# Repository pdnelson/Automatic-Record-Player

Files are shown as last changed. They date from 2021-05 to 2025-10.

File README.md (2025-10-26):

# Automatic Turntable Introduction
This project is currently under construction separately from this repository. This repository is now obsolete, and will be left in a non-functional state.

This is a fully automatic turntable that plays 7", 10" or 12" records! The automatic capabilities are powered by an Arduino Nano Every, 2 stepper motors, and a bunch of sensors.
Some notes on this turntable include (see "Features, User Inputs and Routines" section for more details):
- Stereo RCA outputs for a receiver
  - Includes Ground line
- Able to fit any commercial cartridge
- 16 2/3, 33 1/3, 45 and 78-RPM speeds
  - Digital or analog speed monitoring on 7-segment display or strobe disc, respectively
- Automatic functionality
  - Returns tonearm to "home" position automatically after a record is finished
  - Other buttons that contain other pre-defined routines (play and pause) that the user must initiate
  - Output port to allow another device to execute commands and read statuses
- Standard PC 3-prong female plug in the back to allow hookup to 120v or 230v households
- Counterbalance weight to fine-tune tonearm weight
- Skate/Anti-skate weight to fine-tune horizontal drift

# Demo Videos

I went over some information of this version of the turntable [in this video](https://www.youtube.com/watch?v=k4UXI1rkMYs). Further updates will be referenced on that channel.

# Features, User Inputs and Routines
The turntable has several inputs the user can use. Most of these functions must be initiated by the user by either pressing a button or flipping a switch, though homing can also be done automatically, which will be explained in more detail later on. Routine interrupt is currently not planned. This means that while one routine is running, none of the others can be executed for the duration of the currently-running routine.

## Automatic/manual switch
This is a 3-position switch with the center position being "off." Flipping the switch to the "up" position will set the turntable to automatic, while "down" will set it to manual. The turntable will automatically be homed upon flipping the switch to "automatic." Flipping it to "manual" will home the vertical axis, which will set the tonearm down in place where it currently is. The reason for this inclusion is to account for us not knowing what position the tonearm will be in when the device is turned on.

As soon as this switch is flipped to "manual" or "automatic," the software setup procedure begins.

## Play/Home button
The "play/home" button will pick the tonearm up from any point, and either drop it at the beginning of a record, or at the home position. If the tonearm is past the play position (i.e. on a record), then the button will home the tonearm. Otherwise, the button will drop it at the beginning of a record. These positions are determined using a slotted optical sensor.

## Pause button
The pause button will lift the tonearm up until the pause limit switch becomes "high." 

When the pause button is pressed again, if the tonearm is directly above "home" position, it will be set fown quickly until the lower limit switch becomes "high." Otherwise, if it is NOT over "home," it will be gently set down.

## Speed Selectors
There are two speed selector switches: The main selector switch, and the "alternate" speed button.

The main speed selector switch is a 3-position switch with the center position turning the turntable motor off, the lower position spinning it at 33 1/3-RPM, and the upper position spinning it at 45-RPM. When the "alternate" speed button is pressed, the switch's upper position will spin at 78-RPM, and the lower will spin at 16 2/3 RPM.

## Fine-Tune Speed Adjustment
On the right side of the record player, there are four potentiometers: One for each speed setting. This allows the user to perfectly dial in the speed they are looking to play at.

## Record size selector
The record size selector is a 3-position switch, with the top indicating 12", middle 10" and lower 7" records. This switch activates user-set calibration values for how many steps the tonearm should move past the play sensor to the edge of the record.

## Calibration Button
When the calibration button is pressed, the seven-segment display will display the active calibration value set by the record size selector. This value will indicate the number of steps taken once the tonearm moves past the play sensor during the play routine. In addition to showing the calibration value, this will also cause the pause button to increment the value, and the play button to decrement it. This can be used to fine-tune exact step calibrations, so the tonearm always lands on the correct spot of the record.

Releasing this button will save the setting to the Arduino's EEPROM. If the value is changed, saving will be indicated by the movement status LED flashing briefly.

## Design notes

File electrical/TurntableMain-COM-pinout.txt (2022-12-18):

1 - NC
2 - NC
3 - Output - Repeat button status
4 - Output - GND
5 - Output - Speed switch status
6 - Output - Automatic switch status
7 - Input - Play command
8 - Input - Pause command
9 - Input - Move turntable
10 - Input - Alt. Speed Set
11 - Output - Alt. speed status
12 - Input - Speed set
13 - Output - Pause status
14 - Output - Movement status
15 - Output - 5v
16 - Output - Home status

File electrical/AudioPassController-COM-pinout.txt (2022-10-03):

1 - Audio off (high = off, low = on)
2 - 5v
3 - GND

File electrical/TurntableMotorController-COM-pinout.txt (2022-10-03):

1 - Speed select A
2 - Speed select B
3 - Turntable power logic
4 - GND
5 - 12v in

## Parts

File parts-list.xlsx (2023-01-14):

Part Name/URL | Details | Qty. Included | Qty. Needed | Remaining Qty. | Price (Total) | Seller | Notes
Slotted Optical Sensor (https://www.amazon.com/gp/product/B08977QFK5/ref=ppx_yo_dt_b_asin_title_o07_s02?ie=UTF8&psc=1) |  | 5 | 1 | 4 | $8.99 | Amazon
Female RCA Panel-Mount Plugs (https://www.amazon.com/gp/product/B093YX4L9X/ref=ox_sc_act_image_1?smid=AQNSZ4MS7YO2W&psc=1) |  | 6 | 3 | 3 | $9.99 | Amazon
Dowel Pin (https://www.mcmaster.com/98381A510/) | 4037, 4140 Alloy Steel, 3/16" Diameter, 1" Long | 50 | 1 | 49 | $11.80 | McMaster |  | Total Price: | $675.67
Black-Oxide Alloy Steel Socket Head Screw (https://www.mcmaster.com/91251A106/) | 4-40 Thread Size, 1/4" Long | 100 | 20+ | 80- | $10.63 | McMaster
18-8 Stainless Steel Square Nut (https://www.mcmaster.com/94785A511/) | 4-40 Thread Size | 100 | 20+ | 80- | $13.40 | McMaster
Black-Oxide Alloy Steel Socket Head Screw (https://www.mcmaster.com/91251A108/) | 4-40 Thread Size, 3/8" Long | 100 | 10+ | 90- | $10.46 | McMaster
Brass Decorative Round Head Slotted Screw (https://www.mcmaster.com/92453A081/) | 2-56 Thread Size, 1/2" Long | 100 | 20+ | 80- | $7.13 | McMaster
Low-Strength Steel Square Nut (https://www.mcmaster.com/94855A279/) | Zinc-Plated, 2-56 Thread Size | 100 | 20+ | 80- | $5.86 | McMaster
316 Stainless Steel Washer (https://www.mcmaster.com/90107A003/) | for Number 2 Screw Size, 0.094" ID, 0.25" OD | 100 | 10+ | 90- | $2.73 | McMaster
Multipurpose 6061 Aluminum Round Tube (https://www.mcmaster.com/9056K63-9056K634/) | 0.035" Wall Thickness, 3/8" OD |  | 1 |  | $13.72 | McMaster | 2ft length
Black-Oxide Alloy Steel Socket Head Screw (https://www.mcmaster.com/90044A111/) | 4-40 Thread Size, 1" Long, Fully Threaded | 25 | 1 | 24 | $8.68 | McMaster
Rotary Shaft (https://www.mcmaster.com/1265K64/) | 316 Stainless Steel, 8 mm Diameter, 200 mm Long | 1 | 1 | 0 | $25.53 | McMaster | Must cut approx. in half
8mm Ball Bearings (https://www.amazon.com/Bearings-Skateboard-Shielded-Miniature-Skateboards/dp/B07R7PR72H) |  | 10 | 2 | 8 | $9.95 | Amazon
DPDT On-Off-On Switch (https://www.amazon.com/mts-202-125VAC-Position-Toggle-Switch/dp/B0799KM8T6) |  | 10 | 2 | 8 | $7.99 | Amazon
Bubble Spirit Level (https://www.amazon.com/dp/B07NRG8HX6?psc=1&ref=ppx_yo2_dt_b_product_details) |  | 10 | 1 | 9 | $6.99 | Amazon
KF2510 Connector Kit (https://www.amazon.com/dp/B01M69TKAM?psc=1&ref=ppx_yo2_dt_b_product_details) |  |  |  |  | $11.99 | Amazon
Rainbow Ribbon Cable (https://www.amazon.com/dp/B0775WHBP5?psc=1&ref=ppx_yo2_dt_b_product_details) |  |  |  |  | $14.69 | Amazon
6 Pins Dual Row Sockets for Flat Ribbon Cable (https://www.amazon.com/dp/B00D57XC9Q?psc=1&ref=ppx_yo2_dt_b_product_details) |  | 25 | 2 | 23 | $10.75 | Amazon
8 Pins 2.54mm Socket for Flat Ribbon Cable (https://www.amazon.com/dp/B017CMPM1A?psc=1&ref=ppx_yo2_dt_b_product_details) |  | 25 | 1 | 24 | $10.95 | Amazon
Audio-Technica AT-VM95C Cartridge (https://www.amazon.com/Audio-Technica-AT-VM95C-Moving-Turntable-Cartridge/dp/B07JL2RTBX) |  |  | 1 | 0 | $39.00 | Amazon
Turntable cartridge wires (https://www.amazon.com/gp/product/B08YN2D358/ref=ppx_yo_dt_b_asin_title_o06_s00?ie=UTF8&th=1) |  | 1 (set) | 1 (set) | 0 (sets) | $4.23 | Amazon
Linear Actuator (https://www.amazon.com/Electric-High-Speed-sec-Weight-Intelligent-Automation/dp/B07ZJ4XJZP) | 12v 10mm range | 1 | 1 | 0 | $29.99 | Amazon
Screw Mount AC Power Inlet with Fuse Holder (https://www.amazon.com/CESS-Screw-Mount-Holder-Socket/dp/B01GBW8J8A?s=hi) |  | 4 | 1 | 3 | $7.49 | Amazon
Micro limit switches (https://www.amazon.com/gp/product/B073TYWX86/ref=ppx_yo_dt_b_asin_title_o05_s01?ie=UTF8&psc=1) |  | 25 | 2 | 23 | $6.99 | Amazon
Cherry MX Blue Key switch (https://www.amazon.com/gp/product/B07V4S3QDK/ref=ppx_yo_dt_b_asin_title_o04_s00?ie=UTF8&th=1) |  | 20 | 3 | 17 | $11.99 | Amazon
Rubber bushings for motor mount (https://www.amazon.com/gp/product/B07VNDTCQR/ref=ox_sc_act_title_1?smid=ASV3IVVEECBWP&psc=1) |  |  |  |  | $11.97 | Amazon
5v Stepper Motor set w/ IC (https://www.amazon.com/KOOKYE-28BYJ-48-Stepper-ULN2003-Arduino/dp/B019TOJRC4) | must be 5v version |  | 2 |  | $9.99 | Amazon
Mean Well 12v Power Supply (https://www.amazon.com/MEAN-WELL-RS-25-12-Supply-Single/dp/B00FRBMV3Q) | RS-25-12 12V 2.1 Amp |  | 1 |  | $14.47 | Amazon
LEDs (https://www.amazon.com/ELEGOO-Diffused-Assorted-Colors-Arduino/dp/B0739RYXVC) |  | 3 | 600 | 597 | $12.99 | Amazon
Custom Turntable Belt | ~??? circumference (measured from belt) |  | 1 |  | $35.00 |  | TODO: Price is not exact
2370 Tinted Plexiglass (https://www.amazon.com/gp/product/B07R64KXFB/ref=ppx_yo_dt_b_asin_title_o05_s00?ie=UTF8&psc=1) |  |  |  |  | $10.99 | Amazon | Must cut down to size
Heat shrink tubing (https://www.amazon.com/560PCS-Heat-Shrink-Tubing-Eventronic/dp/B072PCQ2LW?s=industrial) |  |  |  |  | $6.99 | Amazon
High-Temperature Dry-Running 841 Bronze Sleeve Bearing (https://www.mcmaster.com/9368T98/) | for 3/16" Shaft Diameter and 1/4" Housing ID, 1/4" Long |  | 5 |  | $3.35 | McMaster
Isolation Feet (https://www.amazon.com/gp/product/B08GNV4BV1/ref=ewc_pr_img_1?smid=A3DXW0NUYLHI2J&th=1) |  | 4 | 4 | 0 | $14.20 | Amazon
Micro USB B Male to USB B Female (https://www.amazon.com/Traovien-Printer-MacBook-Samsung-Printers/dp/B09CY6K156) |  | 1 | 1 | 0 | $7.58 | Amazon
Rubber O Rings (https://www.amazon.com/dp/B08DWHMH9V?psc=1&ref=ppx_yo2ov_dt_b_product_details) | (1x 2" I/D 2 1/4" O/D) (4x 1/4" I/D 3/8" O/D) |  |  |  | $13.99 | Amazon
MX1508 H-Bridge w/ components (https://www.amazon.com/dp/B075S368Y2?psc=1&ref=ppx_yo2ov_dt_b_product_details) |  | 5 | 1 | 4 | $14.99 | Amazon
DC100 Motor Alone (includes pulley) (https://www.originlive.com/shop/dc100-motor-alone.html) |  | 1 | 1 | 0 | $132.22 | Origin Live
R3-2RS Ball Bearing (https://www.mcmaster.com/60355K861/) | Sealed, Trade Number R3-2RS, for 3/16" Shaft Diameter |  | 3 |  | $11.73 | McMaster
6.3v AC Transformer (https://www.digikey.com/en/products/detail/triad-magnetics/F-313X/5032119) |  | 1 | 1 | 0 | $11.06 | DigiKey
Parallel port (https://www.digikey.com/en/products/detail/norcomp-inc/171-025-103L001/858135) | 171-025-103L001 | 1 | 1 | 0 | $1.69 | DigiKey
Encoder (https://www.digikey.com/en/products/detail/broadcom-limited/HEDS-9700-E50/2219906) |  | 1 | 1 | 0 | $15.42 | DigiKey
Thread (https://www.amazon.com/Singer-150-yard-Purpose-Polyester-Thread/dp/B000PSAMCI) | Only needed for internal anti-skate; any thread will do | 1 | 1 | 0 | $4.26 | Amazon
Music Wire Steel Extension Spring with Loop Ends (https://www.mcmaster.com/5108N117/) |  | 5 | 1 | 4 | $14.92 | McMaster
Corrosion-Resistant Curved Disc Springs (https://www.mcmaster.com/9716K18/) |  | 5 | 1 | 4 | $11.76 | McMaster
Ball Bearing 3/8" shaft diameter (https://www.mcmaster.com/60355K504/) |  |  | 2 |  | $11.78 | McMaster
18-8 Stainless Steel Washer (https://www.mcmaster.com/92141A011/) | for Number 10 Screw Size, 0.203" ID, 0.438" OD | 100 | 1 | 99 | $2.40 | McMaster

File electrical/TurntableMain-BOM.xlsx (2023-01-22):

Label(s) | Type | Value(s) | Part Number | Substitute Part # | Mounting Type | Mount Size/Package | Quantity | Price Est. | Notes
A1 | Arduino Nano Every |  | ABX00028 |  | THT (read notes) | DIP30 | 1 | $10.38 | Developer recommends using 30-pin DIP socket. DE37566 pins may need to be used.
C1, C5, C6, C7, C8, C9, C10, C12, C13, C14, C15, C17, C19, C21, C22, C23, C24 | Ceramic Capacitor | 0.1µF; 35V | C0603C104K4NACAUTO |  | SMD | 0603 | 17 | $1.48
C2, C3 | Electrolytic Capacitor | 100µF; 16v | n/a |  | SMD |  | 2 | -- | Take from MX1508 PCB
C20 | Ceramic Capacitor | 1µF; 16V | 0805YD105KAT2A |  | SMD | 0805 | 1 | $0.24
C4, C11 | Ceramic Capacitor | 10µF; 16V | GCM21BM8EE106KE08L |  | SMD | 0805 | 2 | $1.30
C16, C18 | Ceramic Capacitor | 47nF; 25v | 06033C473KAT2A |  | SMD | 0603 | 2 | $0.20
D1 | Diode |  | n/a |  | SMD |  | 1 | -- | Take from MX1508 PCB
D2 | Schottky Diode | 30v; 3a | B330AF-13 |  | SMD | DO-221AC, SMA | 1 | $0.44
J1 | Screw terminal - 2 pins |  | 691137710002 |  | THT |  | 1 | $0.41
J2 | generic male header - 1 pin (1 row) |  | DE37566 |  | THT |  | 1 | -- | Comes in lot listed on main parts list.
J4 | Generic shrouded header - 6 pins (2 rows) |  | 61200621621 | BHR-06-VUA | THT |  | 1 | $0.48
J3, J5, J9, J10, J11, J13, J14, J15, J17 | male header 2 pin (1 row) |  | KF2510 2-pin |  | THT |  | 9 | -- | Comes in a lot with other KF2510 connectors.
J6 | male header 5 pin (1 row) |  | KF2510 5-pin |  | THT |  | 1 | -- | Comes in a lot with other KF2510 connectors.
J7, J8 | male header 5 pins (1 row) |  | YXQJST-XH 4S |  | THT |  | 2 | -- | Comes in lot listed on main parts list.
J16, J18, J19 | male header - 3 pins (1 row) |  | KF2510 3-pin |  | THT |  | 3 | -- | Comes in a lot with other KF2510 connectors.
J12 | Generic shrouded header - 16 pins (2 rows) |  | SBH11-PBPC-D08-RA-BK |  | THT |  | 1 | $0.73
J20 | male header 4 pins (1 row) |  | KF2510 4-pin |  | THT |  | 1 | -- | Comes in a lot with other KF2510 connectors.
J21 | Generic shrouded header - 8 pins (2 rows) |  | BHR-08-VUA |  | THT |  | 1 | $0.35
R4 | Resistor | 220Ω | n/a |  | SMD | 0805 | 1 | -- | Take from MX1508 PCB
R2, R3, R4, R8, R9, R10, R11, R12, R13, R14, R15, R16 | Resistor | 10kΩ; ±5%; 1/4w | ERJ-PA3F1002V |  | SMD | 0603 | 12 | $1.68
R5, R6, R7 | Resistor | 1kΩ; ±5%; 1/4w | ERJ-PA3J102V |  | SMD | 0603 | 3 | $0.33
U1, U6 | Voltage Regulator - Linear | 5v; 3a | MIC29300-5.0WT | MIC29310-5.0WT | THT | TO220 | 2 | $9.40
U2, U3 | Power/Stepper driver |  | ULN2003A |  | THT (read notes) | DIP16 | 2 | -- | Developer recommends using 16-pin DIP socket
U4 | Motor driver |  | MX1508 |  | SMD |  | 1 | -- | Take from MX1508 PCB
U5 | 8:1 multiplexer |  | CD4051BE |  | THT |  | 1 | $0.79
U7, U10, U11, U12, U13, U14 | "Or" gate | 5v | MC74VHC1G32DTT1G |  | SMD | SC-74A, SOT-753 | 6 | $2.88
U8, U9 | "And" gate |  | SN74AUC1G08DCKR |  | SMD | SC-74A, SOT-753 | 2 | $0.98
U15, U16, U17, U18 | 1:2 demultiplexer |  | SN74LVC1G18DBVR |  | SMD | SOT-23-6 | 4 | $1.64
Total (where applicable): |  |  |  |  |  |  | 82 | $33.71
Notes:
Price estimates are as of 3 Sept. 2022

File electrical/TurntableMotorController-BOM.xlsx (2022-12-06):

Label(s) | Type | Value(s) | Part Number | Substitute Part # | Mounting Type | Mount Size/Package | Quantity | Price Est. | Notes
C1, C3 | Ceramic Capacitor | 10µF; 16V | GCM21BM8EE106KE08L |  | SMD | 0805 | 2 | $1.30
C2 | Ceramic Capacitor | 22µF; 25v | CL21A226MAYNNNE |  | SMD | 0805 | 1 | $0.25
C4 | Ceramic Capacitor | 0.47nF; 50v | 0805B471K500CT |  | SMD | 0805 | 1 | $0.10
C5, C6, C7, C8, C9, C10 | Ceramic Capacitor | 100 nf; 50v | CL21B104KBCNNNC |  | SMD | 0805 | 6 | $0.60
R5, R14, R15 | Resistor | 1kΩ; ±5%; 1/4w | ERJ-PA3J102V |  | SMD | 0603 | 3 | $0.33
R6, R10 | Resistor | 69kΩ | RN73H1JTTD6902D100 |  | SMD | 0603 | 2 | $0.78
R7 | Resistor | 26.7kΩ | RC0603FR-0726K7L |  | SMD | 0603 | 1 | $0.10
R8, R9 | Resistor | 47kΩ | RG1608P-473-B-T5 |  | SMD | 0603 | 2 | $0.76
R11 | Resistor | 104kΩ | RN73H1JTTD1043B50 |  | SMD | 0603 | 1 | $0.53
R12 | Resistor | 94kΩ | RT0603BRD0794K2L |  | SMD | 0603 | 1 | $0.34
R13 | Resistor | 10kΩ; ±5%; 1/4w | ERJ-PA3F1002V |  | SMD | 0603 | 1 | $0.16
U3, U4, U5, U6, U7, U8 | Demultiplexer 1:2 | 12v; 5a | ISL43210IHZ-T7A | DG9431EDV-T1-GE3 | SMD |  | 6 | $17.52
U2 | Variable Voltage Regulator | 12v; 5a | AZ1084CS2-ADJTRE1 |  | SMD |  | 1 | $0.72
D1 | Rectifier Diode |  | 1N4007 |  | THT | 300 mil | 1 | $0.11
Q1 | Basic FET P-Channel |  | TIP120 |  | THT |  | 1 | $1.00
U1 | Voltage Regulator - Linear | 5v; 3a | MIC29300-5.0WT | MIC29310-5.0WT | THT | TO220 | 1 | $4.70
R1, R2, R3, R4 | Thumbwheel Potentiometer | 10kΩ; 1/2w | 3352W-1-103LF |  | THT |  | 4 | $10.00
RL1 | Relay |  | J104D2C5VDC.20S |  | THT | DPDT (2 Form C) | 1 | $1.31
J1, J2, J3, J4 | Screw Terminal |  | 8191 | 36-8191-ND | THT |  | 4 | $2.08
J5 | male header 5 pins (1 row) |  | KF2510 5-pin |  | THT |  | 1 | --
J6 | male header 2 pins (1 row) |  | KF2510 2-pin |  | THT |  | 1 | --
J7 | Screw terminal (2 pins) |  | ED10563-ND |  | THT |  | 1 | $0.41
Total (where applicable): |  |  |  |  |  |  | 42 | $42.69
Notes:
Price estimates are as of 2 Oct. 2022

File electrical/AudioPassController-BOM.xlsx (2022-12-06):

Label(s) | Type | Value(s) | Part Number | Substitute Part # | Mounting Type | Mount Size/Package | Quantity | Price Est. | Notes
C1 | Ceramic Capacitor | 10µF | CL21A106KOQNNNE |  | SMD | 0805 | 1 | $0.10
C2 | Ceramic Capacitor | 1µF | CL21B105KAFNNNE |  | SMD | 0805 | 1 | $0.10
C3 | Ceramic Capacitor | 47nF | CL21B473KBCNNNC |  | SMD | 0805 | 1 | $0.10
C4, C5 | Ceramic Capacitor | 100nF | CL21B104KACNNNC |  | SMD | 0805 | 2 | $0.10
R1, R2 | Resistor | 10kΩ; ±5%; 1/4w | ERJ-PA3F1002V |  | SMD | 0603 | 2 | $0.32
U1, U2 | 1:2 demultiplexer |  | SN74LVC1G18DBVR |  | SMD | SOT-23-6 | 2 | $0.82
J1 | male header - 3 pins (1 row) |  | KF2510 3-pin |  | THT |  | 1 | --
J2 | Screw terminal (4 pins) |  | ED10563-ND |  | THT |  | 1 | $1.45
J3, J4 | male header - 2 pins (1 row) |  | KF2510 2-pin |  | THT |  | 2 | --
Total (where applicable): |  |  |  |  |  |  | 13 | $2.99
Notes:
Price estimates are as of 2 Oct. 2022

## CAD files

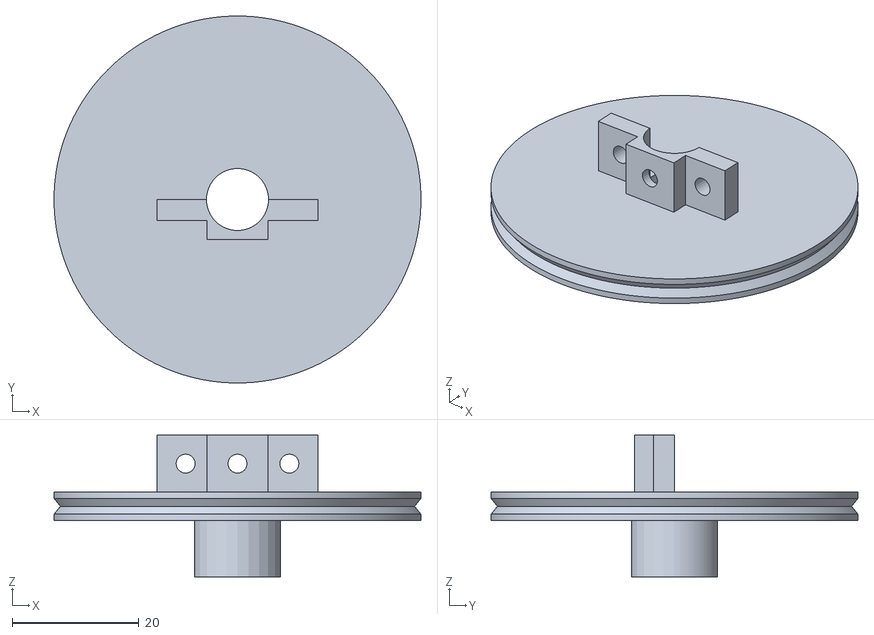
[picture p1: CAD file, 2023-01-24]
3d-models/tonearm-movement-hub/horizontal-movement/main-drive-wheel.stl
58.0 x 58.0 x 22.4

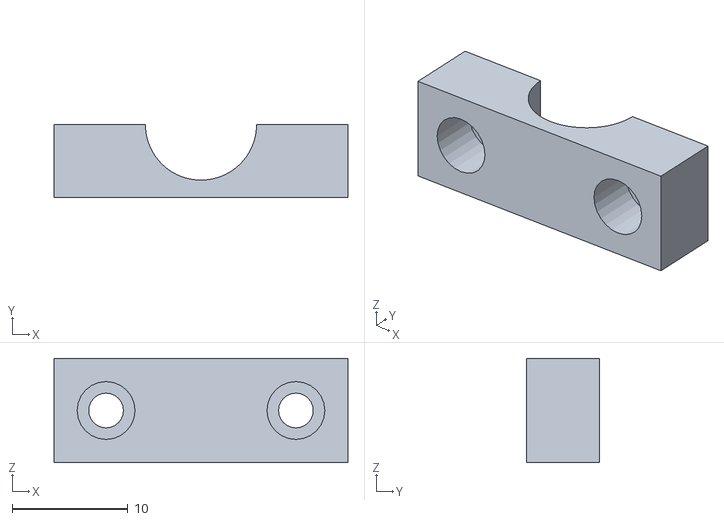
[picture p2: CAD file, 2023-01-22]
3d-models/tonearm-movement-hub/horizontal-movement/main-drive-wheel-fastener.stl
25.4 x 6.30 x 9.00

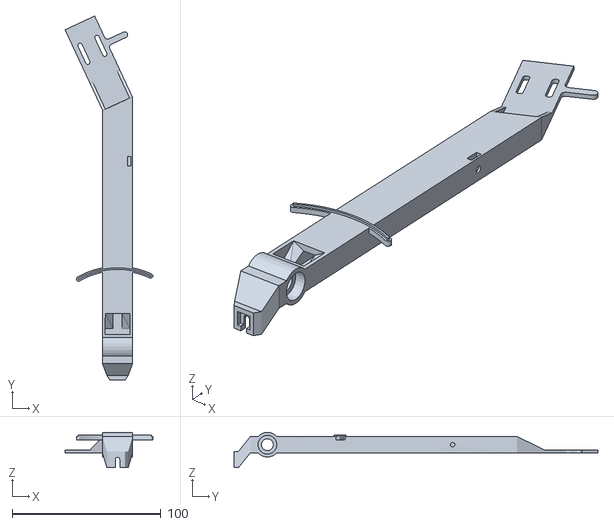
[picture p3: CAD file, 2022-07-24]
3d-models/tonearm/tonearm-full.stl
59.2 x 245.0 x 23.9

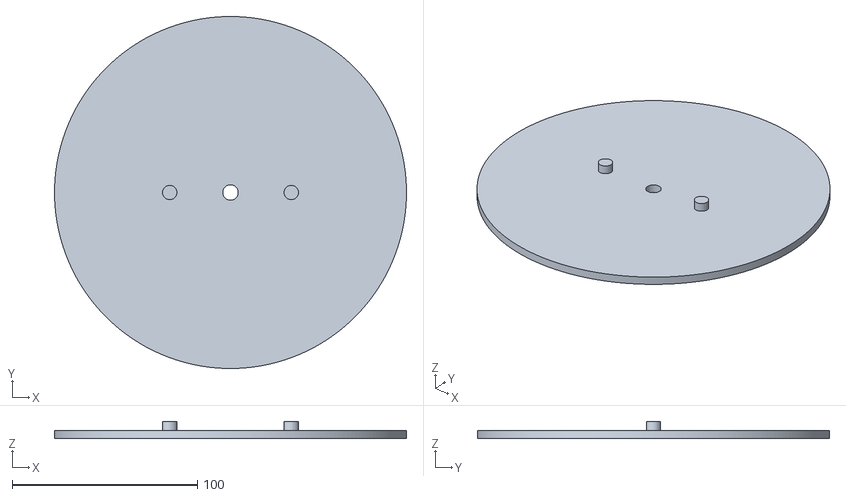
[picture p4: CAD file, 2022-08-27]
3d-models/turntable/turntable/full-platter.stl
190.0 x 190.0 x 9.30

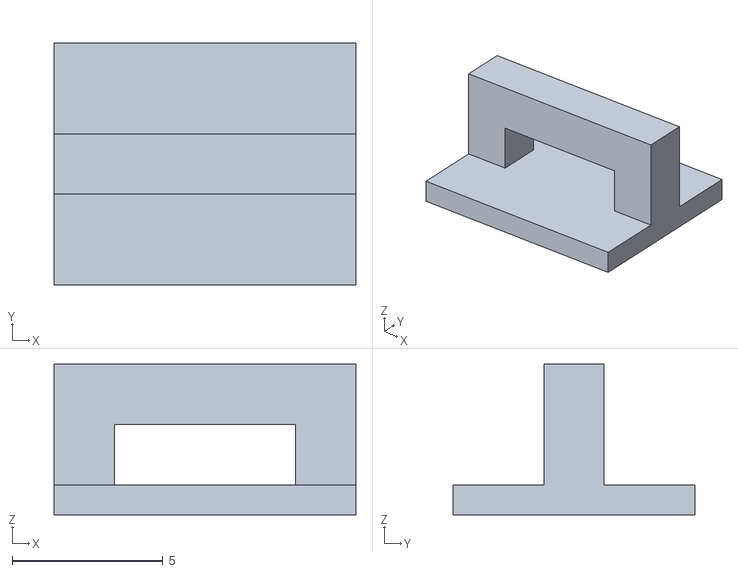
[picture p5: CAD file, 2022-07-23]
3d-models/cable-management-thing.stl
10.0 x 8.00 x 5.00

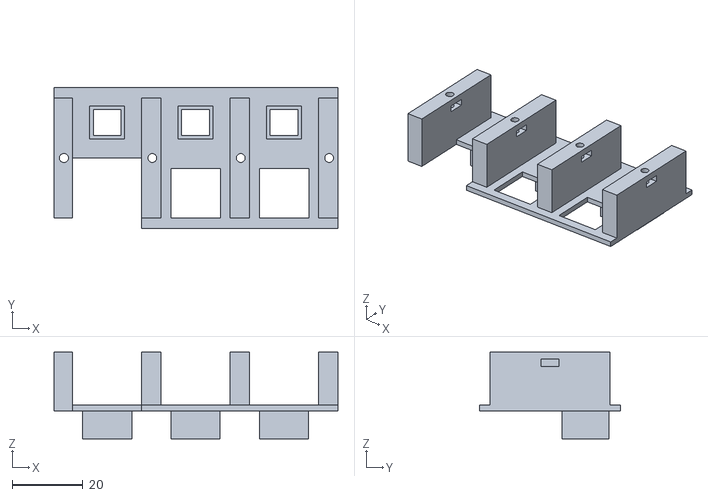
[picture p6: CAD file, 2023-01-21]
3d-models/command-buttons/command-button-holder.stl
80.3 x 40.0 x 24.5

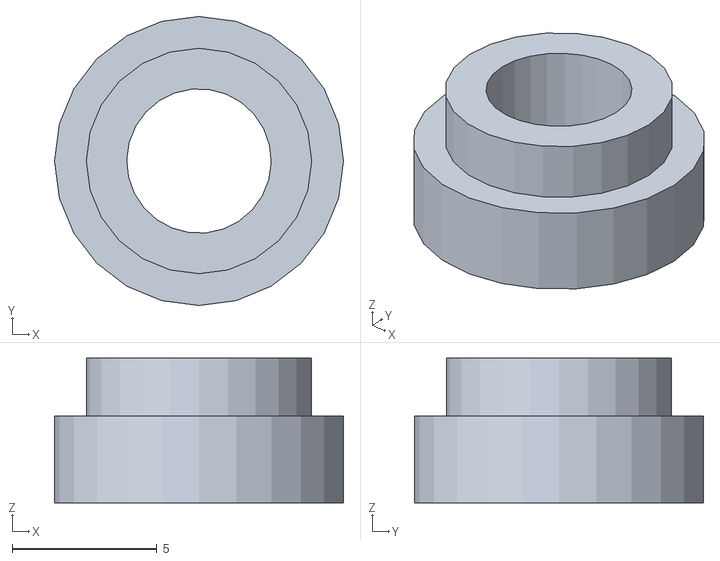
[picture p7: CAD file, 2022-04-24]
3d-models/inner-chassis/ir-sensor-mount/movement-ir-interrupter-spacer.stl
10.00 x 10.0 x 5.00

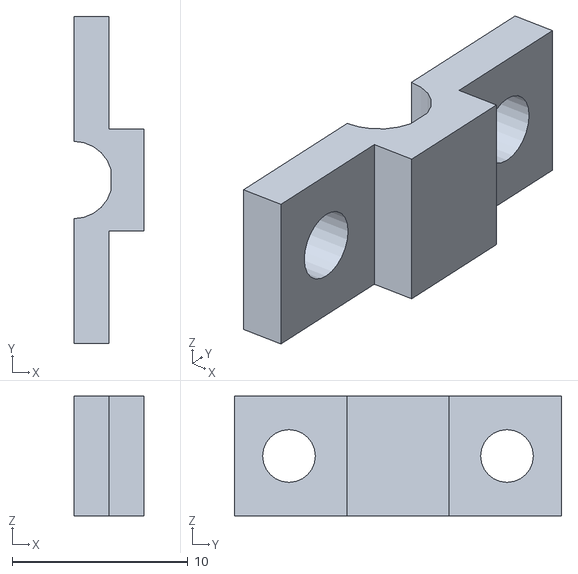
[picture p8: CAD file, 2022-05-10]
3d-models/inner-chassis/tonearm-rod-clip.stl
4.00 x 18.6 x 6.80

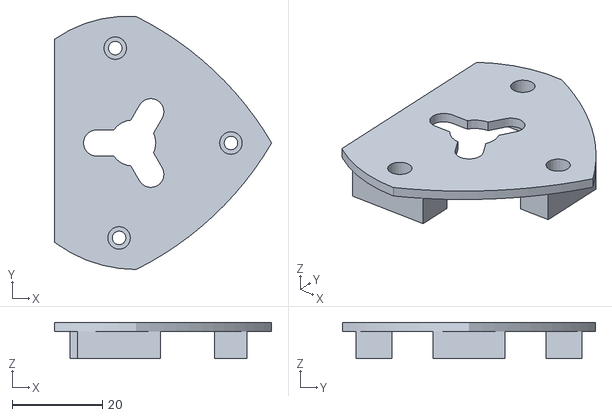
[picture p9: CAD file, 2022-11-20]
3d-models/motor-mount/motor-mount-one-piece-top.stl
48.1 x 56.0 x 8.00

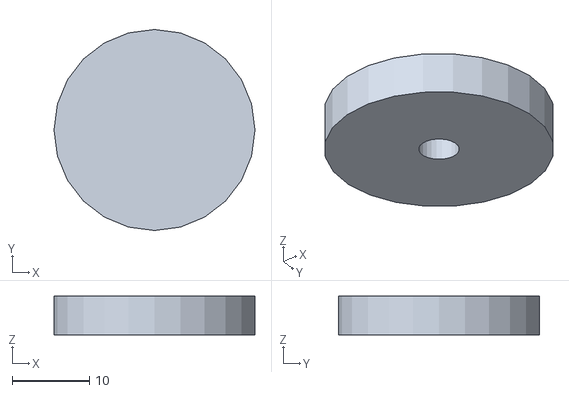
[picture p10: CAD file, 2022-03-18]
3d-models/shell/foot.stl
26.0 x 26.0 x 5.00

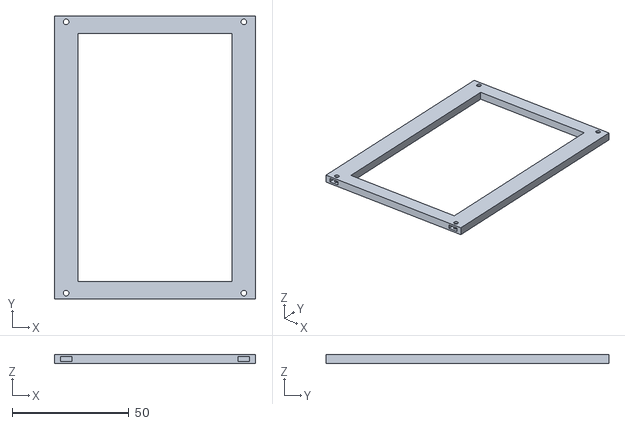
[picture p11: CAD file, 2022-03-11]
3d-models/speed-adjustment-enclosure/speed-adjustment-enclosure-mount.stl
86.0 x 121.0 x 4.00

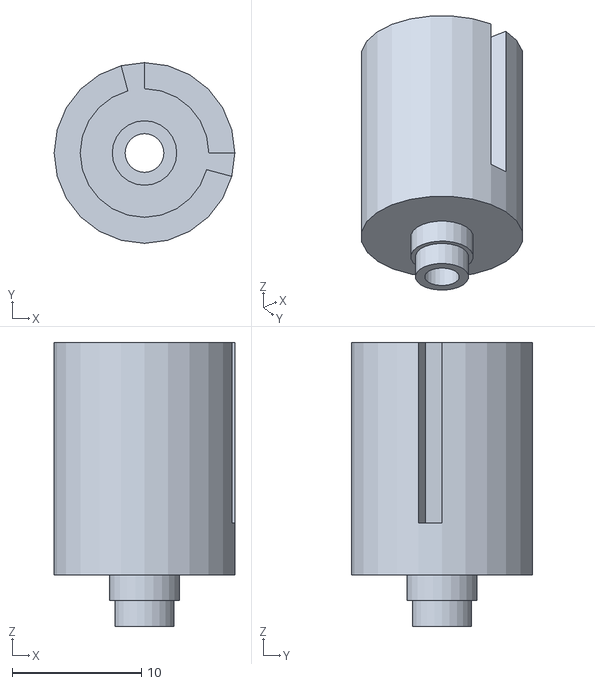
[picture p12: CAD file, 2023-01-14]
3d-models/tonearm-movement-hub/anti-skate/bottom-mechanism.stl
14.0 x 14.0 x 22.0

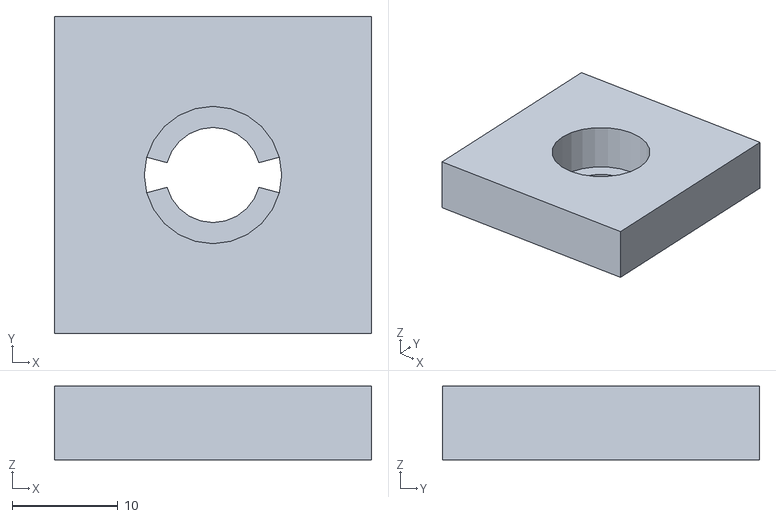
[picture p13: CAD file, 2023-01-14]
3d-models/tonearm-movement-hub/anti-skate/prototype/bearing-holder.stl
30.0 x 30.0 x 7.00

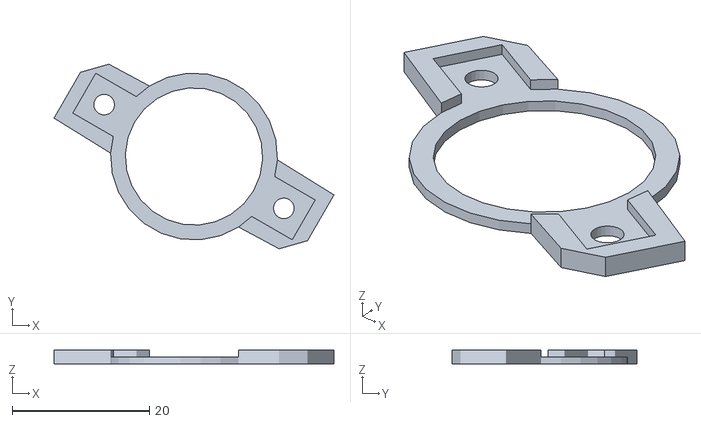
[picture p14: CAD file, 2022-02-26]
3d-models/tonearm-movement-hub/ball-bearing-components/ball-bearing-brace.stl
40.8 x 26.9 x 2.00

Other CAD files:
3d-models/tonearm-movement-hub/horizontal-movement/h-motor-mount/linear-actuator-bracket.stl
3d-models/tonearm-movement-hub/horizontal-movement/horizontal-axis-rod/horizontal-axis-rod-stencil-pt-2.stl
3d-models/tonearm-movement-hub/horizontal-movement/horizontal-axis-rod/prototype/h-axis-rod-prototype.stl
3d-models/tonearm-movement-hub/ir-interrupter/movement-ir-interrupter-fastener.stl
3d-models/cable-management-thing.skp
3d-models/command-buttons/button-cherry.skp
3d-models/command-buttons/button-cherry.stl
3d-models/command-buttons/button-push.skp
3d-models/command-buttons/button-push.stl
3d-models/command-buttons/command-button-holder.skp
3d-models/command-buttons/command-button-stencil.skp
3d-models/command-buttons/command-button-stencil.stl
3d-models/command-buttons/single-command-button-holder.skp
3d-models/command-buttons/single-command-button-holder.stl
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

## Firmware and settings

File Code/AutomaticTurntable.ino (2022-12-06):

#include <Stepper.h>
#include <Multiplexer.h>
#include <DcMotor.h>
#include "proto/AutomaticTurntable.h"
#include "proto/Constants.h"
#include "enums/ArduinoPin.h"
#include "enums/MultiplexerInput.h"
#include "enums/MovementResult.h"
#include "enums/AutoManualSwitchPosition.h"
#include "TonearmMovementController.h"

// Though this is one stepper motor declaration, this object actually handles both the vertical and horizontal
// stepper motors. Which one is currently active is determined by the ArduinoPin::MotorAxisSelector.
Stepper tonearmMotor = Stepper(
  STEPS_PER_REVOLUTION, 
  ArduinoPin::StepperPin4,
  ArduinoPin::StepperPin2, 
  ArduinoPin::StepperPin3, 
  ArduinoPin::StepperPin1
);

// The multiplexer monitors most input values that we read to determine the statuses of various sensors.
Multiplexer mux = Multiplexer(
  ArduinoPin::MuxOutput, 
  ArduinoPin::MuxSelectorA, 
  ArduinoPin::MuxSelectorB, 
  ArduinoPin::MuxSelectorC
);

// The tonearmClutch allows us to engage or disengage the horizontal gearing to either allow for automatic
// movement (engaged), or manual movement (disengaged).
DcMotor horizontalClutch = DcMotor(
  ArduinoPin::HorizontalClutchMotorDir1,
  ArduinoPin::HorizontalClutchMotorDir2
);

// The tonearmController is in charge of automatically moving the tonearm vertically or horizontally.
TonearmMovementController tonearmController = TonearmMovementController(
  mux,
  tonearmMotor,
  ArduinoPin::MotorAxisSelector,
  horizontalClutch,
  MultiplexerInput::VerticalLowerLimit,
  MultiplexerInput::VerticalUpperLimit
);

// All of these fields are used to calculate the speed that the turntable is spinning.
volatile unsigned long currMillisSpeed = millis();
volatile unsigned long lastMillisSpeed = currMillisSpeed;
volatile double currSpeed;

// Used for the pickup sensor
uint8_t consecutivePickupSensorChanges = 0;
bool lastPickupSensorStatus = false;
unsigned long lastMillisPickup = __LONG_MAX__;

bool paused = false;

void setup() { //Serial.begin(SERIAL_SPEED);
  // Set pins
  pinMode(ArduinoPin::MovementStatusLed, OUTPUT);
  pinMode(ArduinoPin::PauseStatusLed, OUTPUT);
  pinMode(ArduinoPin::SpeedSensor, INPUT);
  attachInterrupt(digitalPinToInterrupt(ArduinoPin::SpeedSensor), calculateTurntableSpeed, RISING);

  // Set calibration values
  tonearmController.setClutchEngagementMs(CLUTCH_ENGAGEMENT_MS);
  tonearmController.setTopMotorSpeed(MOVEMENT_RPM_TOP_SPEED);
  tonearmController.setVerticalTimeout(VERTICAL_MOVEMENT_TIMEOUT_STEPS);
  mux.setDelayMicroseconds(MULTIPLEXER_DELAY_MICROS);

  // Engage the horizontal clutch. This will be setting it to the "starting" point for where we know it is engaged
  horizontalClutch.immediateStart(HorizontalClutchPosition::Engage);

  // Begin startup light show
  delay(100);
  digitalWrite(ArduinoPin::PauseStatusLed, LOW);
  digitalWrite(ArduinoPin::MovementStatusLed, HIGH);
  delay(100);
  digitalWrite(ArduinoPin::MovementStatusLed, LOW);
  digitalWrite(ArduinoPin::PauseStatusLed, HIGH);
  delay(100);
  digitalWrite(ArduinoPin::MovementStatusLed, HIGH);
  digitalWrite(ArduinoPin::PauseStatusLed, LOW);
  delay(100);
  digitalWrite(ArduinoPin::MovementStatusLed, LOW);
  // End startup light show

  // Check sensors, and perform an initial movement if necessary.
  MovementResult currentMovementStatus = MovementResult::None;

  bool homeExecuted = false;

  // If the turntable is turned on to "automatic," then home the whole tonearm if it is not already home.
  if(mux.readDigitalValue(MultiplexerInput::AutoManualSwitch) == AutoManualSwitchPosition::Automatic && 
    digitalRead(ArduinoPin::HorizontalHomeOrPlayOpticalSensor)) {
    MovementResult currentMovementStatus = homeRoutine();
    homeExecuted = true;
  }

  // Otherwise, we only want to home the vertical axis if it is not already homed, which will drop the tonearm in its current location.
  else if(!mux.readDigitalValue(MultiplexerInput::VerticalLowerLimit)) {
      currentMovementStatus = pauseOrUnpause();
  }

  // If the movement was anything other than success/none, then it failed, and we must set the error state.
  if(currentMovementStatus != MovementResult::Success && currentMovementStatus != MovementResult::None) {
    setErrorState(currentMovementStatus);
  }

  // If the homing routine was not executed, then the horizontal clutch is still engaged, and we need to disengage it
  if(!homeExecuted) {
    delay(500); // Wait 500ms so the clutch can home the whole way before we disengage it
    tonearmController.setClutchPosition(HorizontalClutchPosition::Disengage);
  }
}

void loop() {
  monitorCommandButtons();
  monitorPickupSensor();
}

// When a command button is pressed (i.e. Home/Play, or Pause/Unpause), then its respective command will be executed.
void monitorCommandButtons() {
  MovementResult currentMovementStatus = MovementResult::None;

  if(mux.readDigitalValue(MultiplexerInput::PauseButton)) {
    currentMovementStatus = pauseOrUnpause();
  }
  
  // If the play/home button is pressed, the command executes
  else if(mux.readDigitalValue(MultiplexerInput::PlayHomeButton)) {

    // If the tonearm is past the location of the home sensor, then this button will home it. Otherwise, it will execute
    // the play routine.
    if(!digitalRead(ArduinoPin::HorizontalHomeOrPlayOpticalSensor)) 
      currentMovementStatus = playRoutine();
    else 
      currentMovementStatus = homeRoutine();
  }

  // If the movement was anything other than success/none, then it failed, and we must set the error state.
  if(currentMovementStatus != MovementResult::Success && currentMovementStatus != MovementResult::None) {
    setErrorState(currentMovementStatus);
  }
}

// Monitor the pickup sensor. If this sensor detects that the tonearm is traveling over the end deadwax of a record, it
// it will execute the homing routine. This will only occur if the auto/manual switch is set to Automatic.
//
// TODO: This method is not very accurate, and results in a lot of misfires (or no-fires). In the future, a smaller
// sensor will need to be used, the interrupter's resolution will need to be increased, and an additional sensor will
// need to be added so that we can determine the direction the tonearm is moving.
//
// Presently, no direction is being checked, so every sensor change is being taken into account, which is problematic 
// because no record's grooves will sit perfectly in the center of a turntable. There will ALWAYS be some degree of 
// wobble, which can happen back and forth over the falling/rising edge of the sensor/interrupter.
void monitorPickupSensor() {
  if(!paused && mux.readDigitalValue(MultiplexerInput::AutoManualSwitch) == AutoManualSwitchPosition::Automatic) {
    bool currPickupSensorStatus = digitalRead(ArduinoPin::PickupEncoderA);
    unsigned long currMillisPickup = millis();

    if(currPickupSensorStatus != lastPickupSensorStatus) {

      // The base values were found through trial on error, so this equation just translates the interval to whatever speed the
      // turntable is currently spinning at.
      double pickupInterval = (TONEARM_PICKUP_BASE_INTERVAL - (TONEARM_PICKUP_BASE_INTERVAL * currSpeed / TONEARM_PICKUP_BASE_SPEED)) + TONEARM_PICKUP_BASE_INTERVAL;

      // Add to the consecutivePickupSensorChanges if we are within the pickup interval and debounce range. Otherwise, reset to 0.
      if((currMillisPickup - lastMillisPickup) > TONEARM_PICKUP_DEBOUNCE_MS && (currMillisPickup - lastMillisPickup) < pickupInterval) {
        consecutivePickupSensorChanges++;
      }
      else {
        consecutivePickupSensorChanges = 0;
      }

      lastMillisPickup = currMillisPickup;
      lastPickupSensorStatus = currPickupSensorStatus;
    }

    // After x consecutive sensor status changes between the debounce and pickup interval, run the homing routine.
    if(consecutivePickupSensorChanges == TONEARM_PICKUP_CONSECUTIVE_SENSOR_CHANGES) {
      MovementResult movementStatus = homeRoutine();

      // If the movement was anything other than success/none, then it failed, and we must set the error state.
      if(movementStatus != MovementResult::Success && movementStatus != MovementResult::None) {
        setErrorState(movementStatus);
      }

      consecutivePickupSensorChanges = 0;
    }
  }
}

// Move the tonearm clockwise to the play sensor
// This is a multi-movement routine, meaning that multiple tonearm movements are executed. If one of those movements fails, the
// whole routine is aborted.
MovementResult playRoutine() {
  digitalWrite(ArduinoPin::MovementStatusLed, HIGH);
  digitalWrite(ArduinoPin::PauseStatusLed, LOW);
  paused = false;

  MovementResult result = MovementResult::None;

  // TODO: Rewrite this using the new play routine.

  digitalWrite(ArduinoPin::MovementStatusLed, LOW);
  
  return result;
}

// Move the tonearm counterclockwise to the home sensor.
// This is a multi-movement routine, meaning that multiple tonearm movements are executed. If one of those movements fails, the
// whole routine is aborted.
MovementResult homeRoutine() {
  digitalWrite(ArduinoPin::MovementStatusLed, HIGH);
  digitalWrite(ArduinoPin::PauseStatusLed, LOW);
  paused = false;

  MovementResult result = MovementResult::None;

  result = tonearmController.moveUp(MOVEMENT_RPM_DEFAULT);
  if(result != MovementResult::Success) return result;

  // TODO: Shut turntable motor off here

  result = tonearmController.horizontalHome();
  if(result != MovementResult::Success) return result;

  result = tonearmController.moveDown(MOVEMENT_RPM_DEFAULT);
  if(result != MovementResult::Success) return result;

  digitalWrite(ArduinoPin::MovementStatusLed, LOW);

  return result;
}

// This is the pause routine that will lift up the tonearm from the record until the user "unpauses" by pressing the
// pause button again
MovementResult pauseOrUnpause() {
  digitalWrite(ArduinoPin::MovementStatusLed, LOW);
  digitalWrite(ArduinoPin::PauseStatusLed, HIGH);
  paused = true;

  MovementResult result = MovementResult::None;

  // If the vertical lower limit is pressed (i.e., the tonearm is vertically homed), then move it up
  if(mux.readDigitalValue(MultiplexerInput::VerticalLowerLimit)) {
    result = tonearmController.moveUp(MOVEMENT_RPM_DEFAULT);
  }

  // Otherwise, just move it down and then shut off the LED
  else {
    uint8_t tonearmSetRpm = 0;

    // If the tonearm is hovering over home position, then just go down at default speed
    if(!digitalRead(ArduinoPin::HorizontalHomeOrPlayOpticalSensor)) {
      tonearmSetRpm = MOVEMENT_RPM_DEFAULT;
    }

    // Otherwise, set it down carefully
    else tonearmSetRpm = MOVEMENT_RPM_CAREFUL;

    result = tonearmController.moveDown(tonearmSetRpm);

    digitalWrite(ArduinoPin::PauseStatusLed, LOW);
    paused = false;
  }

  return result;
}

// Each time the interrupt calls this function, the current milliseconds are polled, and compared against the last polling
// to calculate the speed the turntable is spinning on each rotation. This calculation is always occurring, even if the speed
// is not being displayed.
// This is attached to an interrupt because it is a time-sensitive operation, and having to wait for other code to finish executing
// would cause this to return inaccurate values.
void calculateTurntableSpeed() {
  currMillisSpeed = millis();
  currSpeed = 60000 / (double)(currMillisSpeed - lastMillisSpeed);
  lastMillisSpeed = currMillisSpeed;
}

// This stops all movement and sets the turntable in an error state to prevent damage.
// This will be called if a motor stall has been detected.
// TODO: Re-implement error codes with LED flashes just like in the earliest revisions...
void setErrorState(MovementResult movementResult) {
  digitalWrite(ArduinoPin::PauseStatusLed, HIGH);
  digitalWrite(ArduinoPin::MovementStatusLed, HIGH);

  // Wait for the user to press the Play/Home or Pause/Unpause buttons to break out of the error state
  while(!mux.readDigitalValue(MultiplexerInput::PlayHomeButton) && !mux.readDigitalValue(MultiplexerInput::PauseButton)) { delay(1); }

  // Clear all statuses. Even though technically the next routine should execute right away, there's that 1/10000 chance that the user can
  // release the button quickly enough to break out of the error state, but not yet execute the next command
  digitalWrite(ArduinoPin::PauseStatusLed, LOW);
  digitalWrite(ArduinoPin::MovementStatusLed, LOW);
  paused = false;
}

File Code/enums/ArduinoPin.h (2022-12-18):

#ifndef ARDUINOPIN_H
#define ARDUINOPIN_H

// Each of these values corresponds to a pin on the Arduino Nano Every
enum ArduinoPin : uint8_t {

    // Currently reserved in the event of serial output being needed. This will also assure that there are no errors
    // when uploading to the Arduino while it is connected to the rest of the turntable controller board.
    ReservedSerial0 = 0,

    // Currently reserved in the event of serial output being needed. This will also assure that there are no errors
    // when uploading to the Arduino while it is connected to the rest of the turntable controller board.
    ReservedSerial1 = 1,

    // This is the pin used to select which motor we are moving, using the demultiplexers.
    MotorAxisSelector = 2,

    // This motor pin (4) channels into a 2-channel demultiplexer, so that either the vertical or horizontal motor receives
    // the pulses. Only one of these motors can ever be moving at once.
    StepperPin4 = 3,

    // This motor pin (3) channels into a 2-channel demultiplexer, so that either the vertical or horizontal motor receives
    // the pulses. Only one of these motors can ever be moving at once.
    StepperPin3 = 4,

    // This motor pin (2) channels into a 2-channel demultiplexer, so that either the vertical or horizontal motor receives
    // the pulses. Only one of these motors can ever be moving at once.
    StepperPin2 = 5,

    // This motor pin (1) channels into a 2-channel demultiplexer, so that either the vertical or horizontal motor receives
    // the pulses. Only one of these motors can ever be moving at once.
    StepperPin1 = 6,

    // One (of three) multiplexer selector pins. This is used (with the other pins) to select which device we want
    // to read a value from.
    MuxSelectorC = 7,

    // One (of three) multiplexer selector pins. This is used (with the other pins) to select which device we want
    // to read a value from.
    MuxSelectorB = 8,

    // One (of three) multiplexer selector pins. This is used (with the other pins) to select which device we want
    // to read a value from.
    MuxSelectorA = 9,

    // This is the multiplexer pin that we read values from.
    MuxOutput = 10,

    // Setting this HIGH will cause the the horizontal motor clutch to either engage or disengage. This is used with HorizontalClutchMotorDir2
    // to drive a DC motor through an H-bridge.
    HorizontalClutchMotorDir1 = 11,

    // Setting this HIGH will cause the the horizontal motor clutch to either engage or disengage. This is used with HorizontalClutchMotorDir1
    // to drive a DC motor through an H-bridge.
    HorizontalClutchMotorDir2 = 12,

    // Pin to enable or disable the turntable motor, meaning that once the turntable crosses the home sensor, and this pin is high, it is free to move.
    TurntableMotorEnable = 13,

    // Will be true if the tonearm lift is not touching the tonearm. 
    TonearmLiftFloating = A0,

    // When this is high and auto-return is triggered, instead of homing, it will go to the beginning of the record again.
    RepeatAfterAutoReturn = A1,

    // The "home" or "play" position optical sensor, depending on which direction the tonearm is moving. If the tonearm is moving
    // counter-clockwise, this sensor acts as the "home" sensor, whereas if it is moving clockwise, it acts as the play sensor.
    HorizontalHomeOrPlayOpticalSensor = A2,

    // This is used, in combination with an interrupt, to calculate what speed the turntable is currently spinning at.
    SpeedSensor = A3,

    // Sensor A of the pickup optical sensor, which, when tripped so many times within a certain interval (also depending on B), will 
    // trigger the homing routine.
    PickupEncoderA = A4,

    // Sensor B of the pickup optical sensor, which, when tripped so many times within a certain interval (also depending on B), will 
    // trigger the homing routine.
    PickupEncoderB = A5,

    // Indicator light so we can tell what the turntable is currently doing. This pin will be set HIGH if the turntable
    // is currently executing the "home" or "play" routine.
    MovementStatusLed = A6,

    // Indicator light so we can tell what the turntable is currently doing. This pin will be set HIGH if the turntable
    // is currently executing the "pause" routine, or if the tonearm is currently in the "pause" position.
    PauseStatusLed = A7
};

#endif

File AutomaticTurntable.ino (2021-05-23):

#include <Stepper.h>

#define SERIAL_SPEED 115200

const int stepsPerRevolution = 2048;

// First stepper motor
#define STEPPER_1_PIN1 2
#define STEPPER_1_PIN2 3
#define STEPPER_1_PIN3 4
#define STEPPER_1_PIN4 5
Stepper motor1 = Stepper(stepsPerRevolution, STEPPER_1_PIN1, STEPPER_1_PIN3, STEPPER_1_PIN2, STEPPER_1_PIN4);

// Second stepper motor
#define STEPPER_2_PIN1 13
#define STEPPER_2_PIN2 12
#define STEPPER_2_PIN3 11
#define STEPPER_2_PIN4 10
Stepper motor2 = Stepper(stepsPerRevolution, STEPPER_2_PIN1, STEPPER_2_PIN3, STEPPER_2_PIN2, STEPPER_2_PIN4);

// Left/right buttons for clockwise/counterclockwise test movements. These exist for troubleshooting/testing purposes only.
#define LEFT_BUTTON 6
#define RIGHT_BUTTON 7

// These LEDs light up when moving one direction or another. They exist for troubleshooting/testing purposes only.
#define MOV_LED_L 8
#define MOV_LED_R 9

// This is an internal step count for the motors, so we know how many steps it has taken
int32_t totalStepCount = 0;
int8_t stepPosition = 0;

// This is the move delay, in ms, between motor steps. The motors used in this project are 28BYJ-48 stepper motors,
// which offer a minimum delay of 2ms between steps. Additional ms were added for precision, at the cost of speed.
int movementRPM = 9;

void setup() {
  pinMode(STEPPER_1_PIN1, OUTPUT);
  pinMode(STEPPER_1_PIN2, OUTPUT);
  pinMode(STEPPER_1_PIN3, OUTPUT);
  pinMode(STEPPER_1_PIN4, OUTPUT);
  motor1.setSpeed(movementRPM);
  
  pinMode(STEPPER_2_PIN1, OUTPUT);
  pinMode(STEPPER_2_PIN2, OUTPUT);
  pinMode(STEPPER_2_PIN3, OUTPUT);
  pinMode(STEPPER_2_PIN4, OUTPUT);
  motor2.setSpeed(movementRPM);
  
  pinMode(LEFT_BUTTON, INPUT);
  pinMode(RIGHT_BUTTON, INPUT);

  pinMode(MOV_LED_L, OUTPUT);
  pinMode(MOV_LED_R, OUTPUT);

  Serial.begin(SERIAL_SPEED);
}

void loop() {
  int leftButtonStatus = digitalRead(LEFT_BUTTON);
  int rightButtonStatus = digitalRead(RIGHT_BUTTON);

  // If the left button is pressed, move clockwise and light the left LED
  if(leftButtonStatus && !rightButtonStatus) {
    digitalWrite(MOV_LED_L, HIGH);
    digitalWrite(MOV_LED_R, LOW);
    motor1.step(1);
    motor2.step(1);
  }

  // If the right button is pressed, move counterclockwise and light the right LED
  else if (!leftButtonStatus && rightButtonStatus) {
    digitalWrite(MOV_LED_L, LOW);
    digitalWrite(MOV_LED_R, HIGH);
    motor1.step(-1);
    motor2.step(-1);
  }
  
  // No movement, so shut the LEDs off
  else {
    digitalWrite(MOV_LED_L, LOW);
    digitalWrite(MOV_LED_R, LOW);
  }
}

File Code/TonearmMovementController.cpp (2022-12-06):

// This library is made specifically for automatic turntable firmware/hardware designed by Patrick Nelson.
// It may have other uses outside of the specific scenarios where it is used here, but that should
// be investigated on an individual basis by whoever stumbles upon this code.

#include "TonearmMovementController.h"

TonearmMovementController::TonearmMovementController(
  Multiplexer inputMux, 
  Stepper tonearmMotors, 
  uint8_t motorSelectPin, 
  DcMotor horizontalClutch, 
  uint8_t verticalLowerLimit, 
  uint8_t verticalUpperLimit
  ):  inputMux(inputMux), 
      tonearmMotors(tonearmMotors),
      horizontalClutch(horizontalClutch)
{
    this->motorSelectPin = motorSelectPin;
    pinMode(motorSelectPin, OUTPUT);

    this->verticalLowerLimit = verticalLowerLimit;
    this->verticalUpperLimit = verticalUpperLimit;

    this->clutchEngagementMs = 0;
    this->topMotorSpeed = 0;
    this->verticalTimeout = 0;
}

MovementResult TonearmMovementController::moveUp(uint8_t speed) {
  this->verticalMove(VerticalMovementDirection::Up, speed);
}

MovementResult TonearmMovementController::moveDown(uint8_t speed) {
  this->verticalMove(VerticalMovementDirection::Down, speed);
}

MovementResult TonearmMovementController::seekRecordEdge() {
  // TODO: Implement
}

MovementResult TonearmMovementController::horizontalHome() {
  // TODO: Implement
}

// Moves the tonearm to a specified destination.
// TODO: Delete this method when we are ready to replace it with seekRecordEdge and horizontalHome
MovementResult TonearmMovementController::moveTonearmHorizontally(uint8_t destinationSensor, unsigned int timeout, int calibration, uint8_t speed) {
    // Select horizontal movement.
    digitalWrite(this->motorSelectPin, MotorAxis::Horizontal);

    // Set values needed for movement.
    unsigned int movementStepCount = 0;
    this->tonearmMotors.setSpeed(speed);
    bool currentSensorStatus = digitalRead(destinationSensor); 

    // Determine what direction we're moving.
    HorizontalMovementDirection movementDirection = currentSensorStatus ? HorizontalMovementDirection::Counterclockwise : HorizontalMovementDirection::Clockwise;

    // Engage clutch so gears can move the tonearm.
    this->setClutchPosition(HorizontalClutchPosition::Engage);

    // Keep moving until the sensor is the opposite of what it started at.
    while(digitalRead(destinationSensor) == currentSensorStatus) {
      this->tonearmMotors.step(movementDirection);

      // If the sensor isn't hit within the expected number of steps, the movement failed.
      if(movementStepCount++ >= timeout) {
        this->setClutchPosition(HorizontalClutchPosition::Disengage);

        if(movementDirection == HorizontalMovementDirection::Clockwise)
          return MovementResult::HorizontalClockwiseDirectionError;

        else
          return MovementResult::HorizontalCounterclockwiseDirectionError;
      }
    }

    this->horizontalRelativeMove(calibration, 14, movementDirection);

    delay(200);

    this->releaseCurrentFromMotors();
    this->setClutchPosition(HorizontalClutchPosition::Disengage);

    return MovementResult::Success;
}

MovementResult TonearmMovementController::verticalMove(VerticalMovementDirection direction, uint8_t speed) {
  // Determine the destination sensor based on the direction passed.
  uint8_t destinationSensor = (direction == VerticalMovementDirection::Up) ? this->verticalUpperLimit : this->verticalLowerLimit;

  // Only perform the operation if the tonearm is not already at its destination.
  if(!this->inputMux.readDigitalValue(destinationSensor)) {
    // Select vertical movement.
    digitalWrite(this->motorSelectPin, MotorAxis::Vertical);

    // Set values needed for movement.
    unsigned int movementStepCount = 0;
    this->tonearmMotors.setSpeed(speed);

    // Move the vertical axis until it reaches its destination.
    while(!this->inputMux.readDigitalValue(destinationSensor)) {
      this->tonearmMotors.step(direction);

      // If the limit isn't hit within the expected number of steps, the movement failed.
      if(movementStepCount++ >= this->verticalTimeout) {
        this->releaseCurrentFromMotors();
        if(direction == VerticalMovementDirection::Up)
          return MovementResult::VerticalPositiveDirectionError;

        else
          return MovementResult::VerticalNegativeDirectionError;
      }
    }

    this->releaseCurrentFromMotors();
  }

  return MovementResult::Success;
}

// This method assumes that the horizontal clutch has already been engaged.
void TonearmMovementController::horizontalRelativeMove(uint16_t steps, uint8_t speed, HorizontalMovementDirection direction) {
  // Select horizontal movement.
  digitalWrite(this->motorSelectPin, MotorAxis::Horizontal);

  // Set values needed for movement.
  unsigned int movementStepCount = 0;
  this->tonearmMotors.setSpeed(speed);

  // Move the tonearm by the number of steps passed as an argument.
  while(movementStepCount++ < steps) {
    this->tonearmMotors.step(direction);
  }

  this->releaseCurrentFromMotors();
}

// This is used to release current from both motors so they aren't drawing power when not in use.
void TonearmMovementController::releaseCurrentFromMotors() {
    this->tonearmMotors.releaseMotorCurrent();
    digitalWrite(this->motorSelectPin, LOW);
}

void TonearmMovementController::setClutchPosition(HorizontalClutchPosition position) {
    this->horizontalClutch.immediateStart(position);

    if(position == HorizontalClutchPosition::Disengage) {
      delay(this->clutchEngagementMs);
    }
    else {
      // Give the clutch additional time to engage because it may not always land in the same spot when disengaging for x ms
      delay(this->clutchEngagementMs + (this->clutchEngagementMs / 2));
    }
    
    this->horizontalClutch.immediateStop();
}

void TonearmMovementController::setClutchEngagementMs(uint16_t ms) {
  this->clutchEngagementMs = ms;
}

void TonearmMovementController::setTopMotorSpeed(uint8_t topSpeed) {
  this->topMotorSpeed = topSpeed;
}

void TonearmMovementController::setVerticalTimeout(unsigned int timeout) {
  this->verticalTimeout = timeout;
}

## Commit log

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2021-05-23 Now utilizing Stepper library instead of my buggy implementation
    [AutomaticTurntable.ino]
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2021-05-28 fixed pins 1 and 2 not working; added comments
    [AutomaticTurntable.ino]
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2021-05-28 added rough tonearm prototype
    [tonearm.skp, tonearm.stl]
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2021-05-29 implemented vertical error checking and error codes
    [AutomaticTurntable.ino]
2021-05-29 added more error checks and skeleton code for home/play
    [AutomaticTurntable.ino]
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2021-05-29 fixed pause routine bug and added flowchart
    [AutomaticTurntable.ino]
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2021-06-11 Updated tonearm model to allow vertical pivot
    [tonearm.skp, tonearm.stl]
2021-06-11 added horizontal tonearm axis model
    [horizontal-axis.skp, horizontal-axis.stl]
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2021-07-25 Added and updated a bunch of 3D models
    [ball-bearing-adapter.skp, ball-bearing-adapter.stl, ball.skp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]
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2021-08-22 fixed bug where pickup routine would execute at the wrong time
    [AutomaticTurntable.ino]
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2021-11-06 Reset is no longer required after error code.
    Issue #1
    Please enter the commit message for your changes. Lines starting
    [AutomaticTurntable.ino]
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2021-12-06 Redesigned turntable to be slightly larger to fit belt
    [motor-mount.skp, motor-mount.stl, mount-template.skp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]
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2021-12-28 Updated software to match hardware errors
    [AutomaticTurntable.ino]
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2021-12-30 updated models and fixed a bug
    [motor-gear-v.skp, motor-gear-v.stl, vertical-gear-rev-2.skp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]
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2022-01-02 Fixed bug where vertical error wasn't releasing motor current
    [TonearmMovementController.cpp]
2022-01-04 Updated PCB to fix errors
    [AutoTurntable.fzz]
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2022-02-02 Finalized PCB redesign
    [AutoTurntable.fzz]
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2022-02-05 Updated BOM - still need to add substitute parts
    [AutoTurntable.fzz, BOM.xlsx]
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2022-02-19 the commit of shame - changed auto/manual input from broken mux pins
    [MultiplexerInput.h]
2022-02-19 Made PCB adjustments to remove separate 5v power
    [AutoTurntable.fzz, BOM.xlsx]
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2022-02-22 Fixed breadboard in electrical
    [AutoTurntable.fzz]
2022-02-23 Replaced THT demux with 4 SMD demuxes to reduce cost
    [AutoTurntable.fzz, BOM.xlsx]
2022-02-23 Updated readme to fix multiplexer input
    [AutoTurntable.fzz]
2022-02-25 Re-added sleeve bearing for tonearm; includes tonearm rod updates
    [ball-bearing-adapter-gear.skp, ball-bearing-adapter-gear.stl, ball-bearing-brace.skp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]
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2022-03-17 Moving parts of under mount are now covered
    [optical-sensor-speed-interrupter.skp, optical-sensor-speed-interrupter.stl, under-mount-rev-2.skp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]
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2022-03-20 Address issues discovered after PCB revision testing
    [AutoTurntable.fzz, BOM.xlsx]
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2022-03-25 Revised the tonearm lift to allow easier adjustment
    [tonearm-lift-rev-3.skp, tonearm-lift-rev-3.stl]
2022-03-25 Revised anti-skate model to allow for easier "0" adjustment
    [anti-skate.skp, anti-skate.stl]
2022-03-25 Revert "Updated setup routine to ONLY vertically home the tonearm"
    This reverts commit 5719bc44494ddf5e0e358e1378353e0531bbddb2.
    [AutomaticTurntable.ino]
2022-03-27 Made speed adj. enclosure work with more potentiometers
    [speed-adjustment-enclosure.skp, speed-adjustment-enclosure.stl]
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2022-04-18 Shortened length of solenoid contact point on middle gear holder
    [middle-gear-holder.skp, middle-gear-holder.stl]
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2022-04-24 Added additional guide lines to the top enclosure
    [top-full-size.skp]
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2022-04-30 Tonearm movement will now have one reference point
    [ir-sensor-mount.skp, ir-sensor-mount.stl, middle-gear-holder.skp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]
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2022-05-04 bringing back middle gear since I accidentally overwrote it
    [main-drive-gear.skp, main-drive-gear.stl, middle-gear.skp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]
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2022-06-14 Horizontal Movement Version 3 - Solenoid now directly pushes motor
    [dowel-pin-cap.skp, dowel-pin-cap.stl, drive-gear-clip.skp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]
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2022-07-03 Simplified turntable design - now takes different platters
    [full-platter.skp, full-platter.stl, record-grip.skp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]
2022-07-10 Combined inner chassis and sensor mount into tonearm movement hub
    [ball-bearing-adapter.skp, ball-bearing-adapter.stl, ball-bearing-brace.skp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]
2022-07-10 Flipped home/play optical sensor
    [AutomaticTurntable.ino]
2022-07-11 Removed inverter between home sensor & and gate
    [AutoTurntable.fzz]
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2022-07-23 Code now accounts for calibration correctly with new setup
    [AutomaticTurntable.ino, Constants.h, TonearmMovementController.cpp]
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2022-07-28 Updated linear actuator bracket to let screws go deeper
    [linear-actuator-bracket.skp, linear-actuator-bracket.stl]
2022-08-01 Updated horizontal gearing to take rubber O rings instead
    [main-drive-gear.skp, main-drive-gear.stl, main-drive-wheel-fastener.skp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]
2022-08-01 Updated vertical movement to use rubber O rings instead of gears
    [motor-gear-v.skp, motor-gear-v.stl, motor-wheel-v.skp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]
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2022-08-18 Reworked horizontal sensor
    [lower-ball-bearing-adapter.skp, lower-ball-bearing-adapter.stl, main-drive-wheel-spacer.skp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]
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2022-08-28 Added PCB components and made code changes to accommodate
    [AutoTurntable.fzz]
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2022-10-25 PCB v5 and code changes to go with
    [TurntableMain.fzz]
2022-11-15 Removed second pulley; motor now turns one giant fly-wheel
    [belt-pulley.skp, belt-pulley.stl, center-piece.skp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]
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2022-11-20 Fix grounding issue on AudioPassController
    [AudioPassController.fzz]
2022-11-20 Update motor mount to add stability with belt tension
    [motor-mount-isolator.skp, motor-mount-isolator.stl, motor-mount-one-piece-top.skp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]
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2022-11-20 Split out strobe circuit into its own module
    [StrobeController-BOM.xlsx, StrobeController.fzz, TurntableMain-BOM.xlsx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]
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2022-12-04 Fix clockwise/counterclockwise direction mixup
    [TonearmMovementController.cpp]
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2022-12-05 Tweak tonearm headshell to have more front space
    [headshell-only.skp, headshell-only.stl]
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2022-12-06 Revise audio controller board to use demultiplexers instead of relay
    [AudioPassController-BOM.xlsx, AudioPassController.fzz]
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2022-12-17 Finish PCB 0.5 - still need to do BOM
    [TurntableMain.fzz, headshell-only.skp, headshell-only.stl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]
2022-12-17 Sensor interrupter now has codewheel to capture entire tonearm movement
    [encoder-interrupter.skp, encoder-interrupter.stl, movement-ir-interrupter-v2.skp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]
2022-12-17 not sure what changed here but I'm saving it
    [TurntableMain.fzz]
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2022-12-18 Create model where codewheel is part of the interrupter
    [movement-ir-interrupter-with-codewheel.skp, movement-ir-interrupter-with-codewheel.stl, test-interrupter-full-codewheel.skp]
2022-12-18 Add missing features to PCB including the following:
    - Repeat
    - Lift indicator
    - Software indication of target speed
    - Move main speed switch indication from software to logic gate
    [TurntableMain.fzz]
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2023-01-07 Fit encoder on test setup - still need to transfer to movement hub
    [encoder-codewheel.skp, encoder-codewheel.stl, encoder-test-setup.skp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]
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2023-01-14 Prototype new anti-skate mechanism - still need to add to movement hub
    [bearing-holder.skp, bearing-holder.stl, bottom-mechanism.skp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]
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2023-01-15 Replace power switch with automatic button
    [TurntableMain.fzz]
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2023-01-17 Modify command button holders to take new buttons
    [command-button-holder.skp, command-button-holder.stl, command-button-stencil.skp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]
2023-01-17 Tweak all 2-pin outputs to have the same polarity
    [TurntableMain.fzz]
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2023-01-21 Did something to the command button holder, but don't remember what
    [command-button-holder.skp, command-button-holder.stl]
2023-01-22 Update main BOM to account for PCB changes
    [TurntableMain-BOM.xlsx, TurntableMain.fzz]
2023-01-22 Modify horizontal movement parts to support larger center tube
    [main-drive-wheel-fastener.skp, main-drive-wheel-fastener.stl, main-drive-wheel-spacer.skp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]
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2023-05-30 I did this stuff months ago and I don't remember what it was
    [h-axis-rod-prototype.skp, h-axis-rod-prototype.stl, horizontal-axis-rod-stencil-pt-1.skp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]
